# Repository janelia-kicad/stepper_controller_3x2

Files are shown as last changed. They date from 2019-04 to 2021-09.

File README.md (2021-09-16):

- [Repository Information](#orgc9c7126)
  - [Description](#org623a5bf)
- [Images](#org1e7d118)
- [Schematic](#org1bed005)
- [Gerbers](#orga20a872)
- [Bill of Materials](#orgaaed6d6)
  - [PCB Parts](#org5e94890)
  - [Supplemental Parts](#org4c9b4c5)
  - [Vendor Parts Lists](#orge23b973)
- [Supplemental Documentation](#org541ab7a)
  - [Assembly Instructions](#org2701e28)

# Repository Information

-   **Name:** stepper\_controller\_3x2
-   **Version:** 1.2
-   **License:** Open-Source Hardware
-   **URL:** <https://github.com/janelia-kicad/stepper_controller_3x2>
-   **Author:** Peter Polidoro
-   **Email:** peter@polidoro.io

## Description

This board controls 1 stepper motor with optional forward and reverse limit switches.

# Images

# Schematic

[./schematic/stepper\_controller\_3x2.pdf](./schematic/stepper_controller_3x2.pdf)

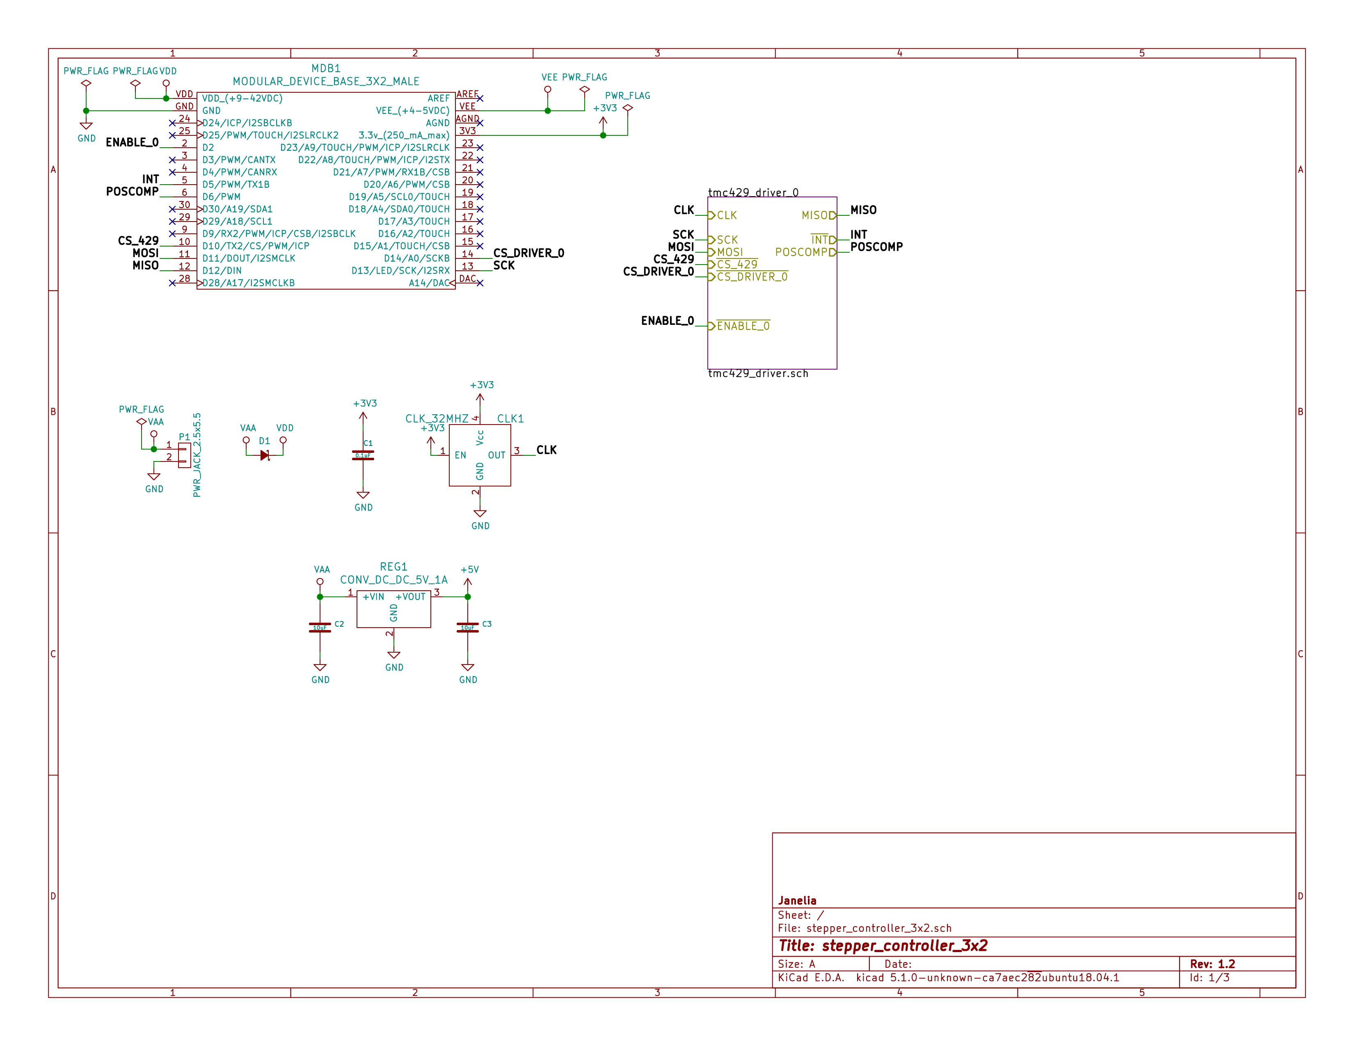
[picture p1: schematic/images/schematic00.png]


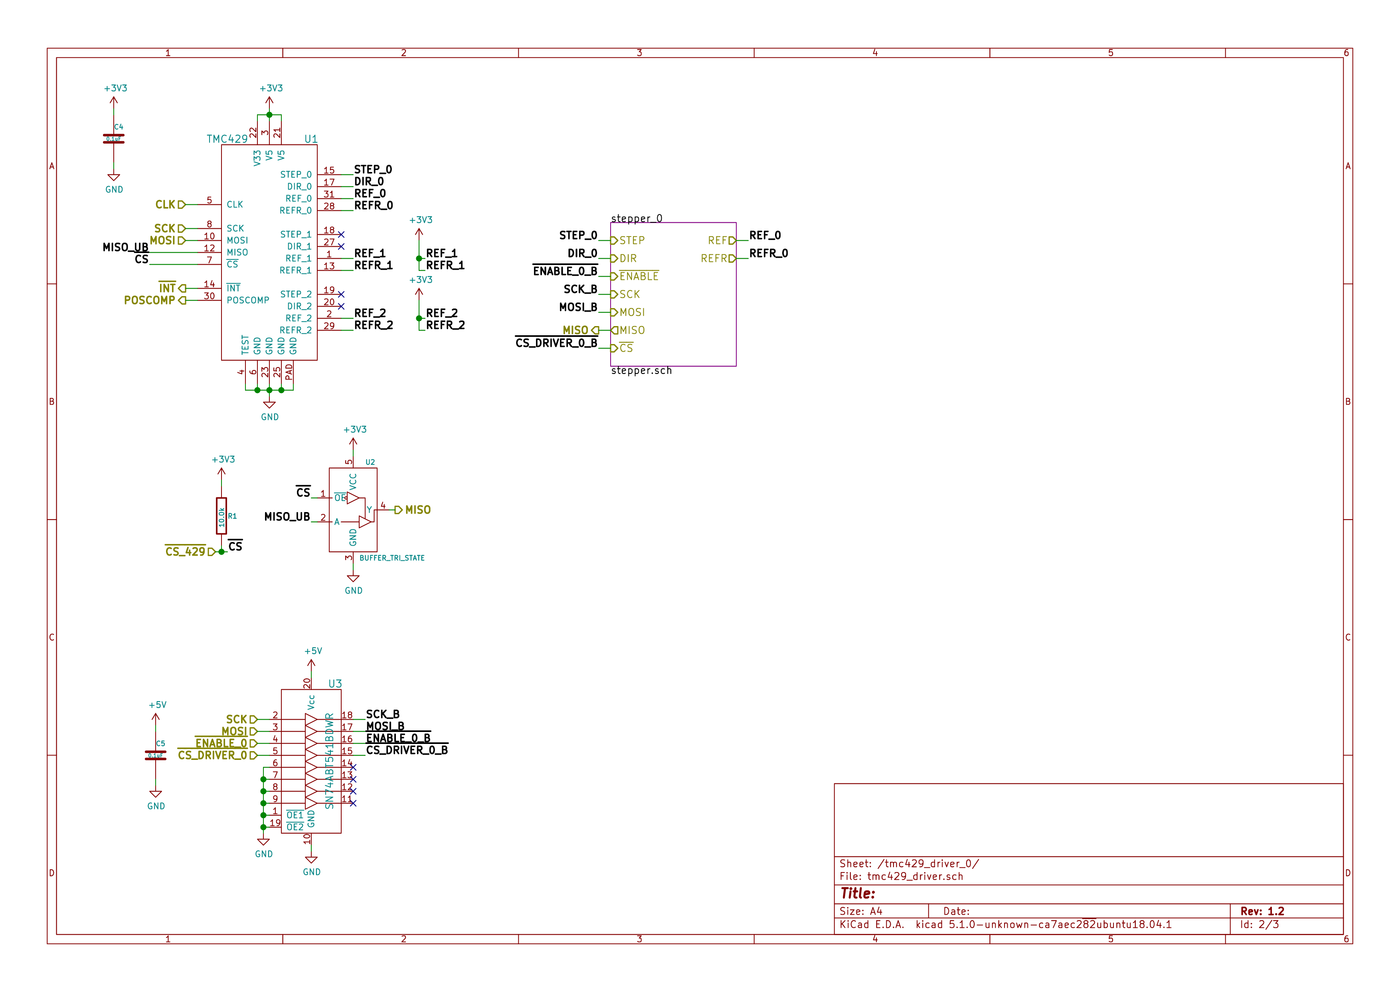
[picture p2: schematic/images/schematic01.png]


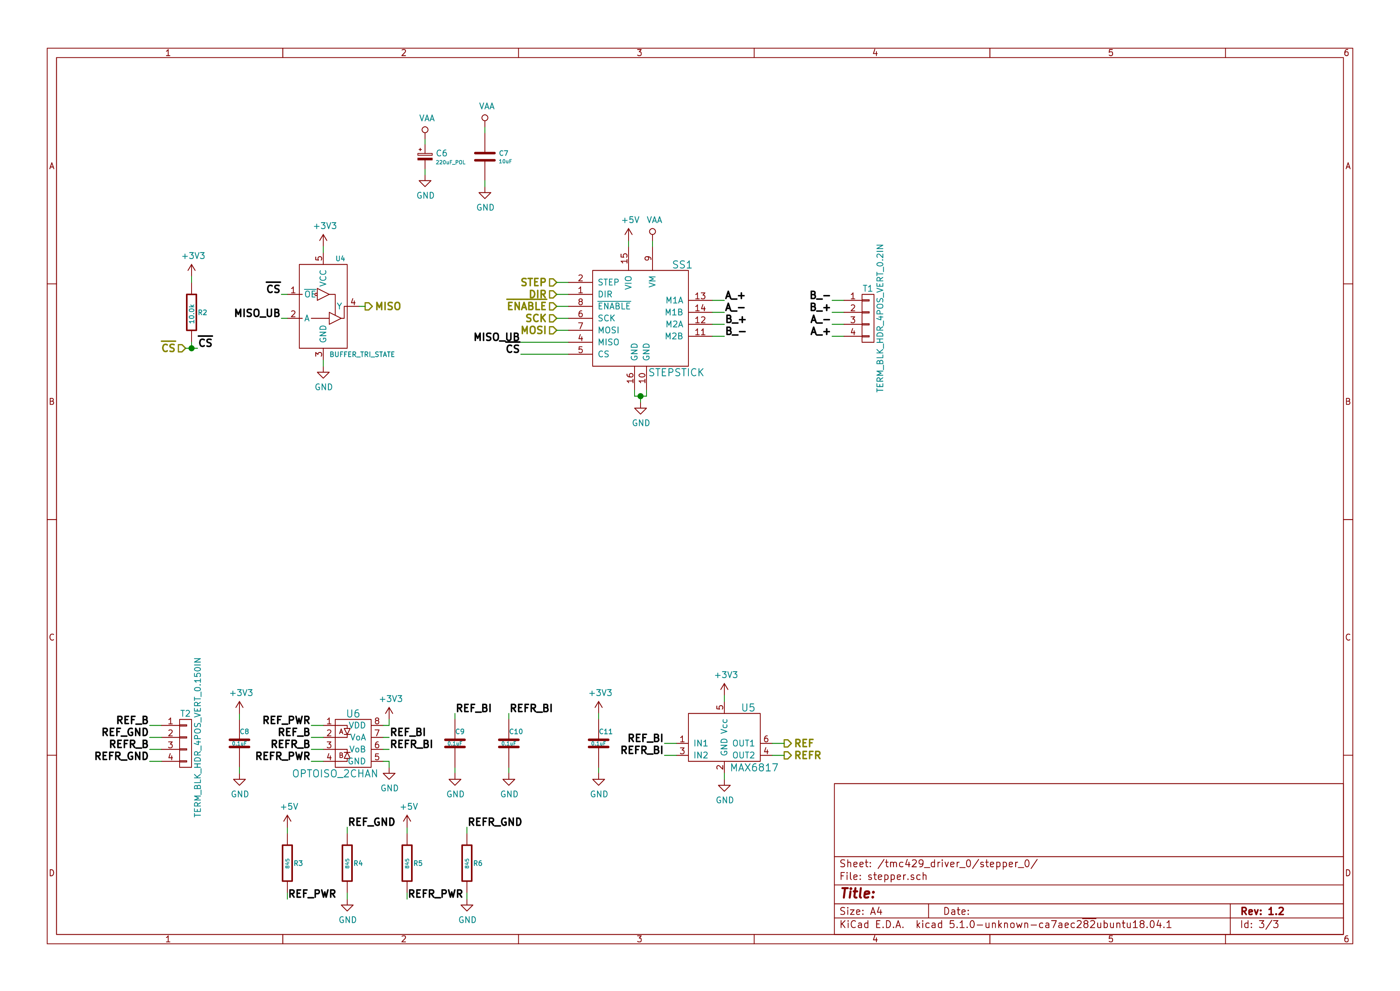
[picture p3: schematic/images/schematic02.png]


# Gerbers

Send gerbers zip file to your favorite PCB manufacturer for fabrication.

[./gerbers/stepper\_controller\_3x2\_v1.2.zip](./gerbers/stepper_controller_3x2_v1.2.zip)

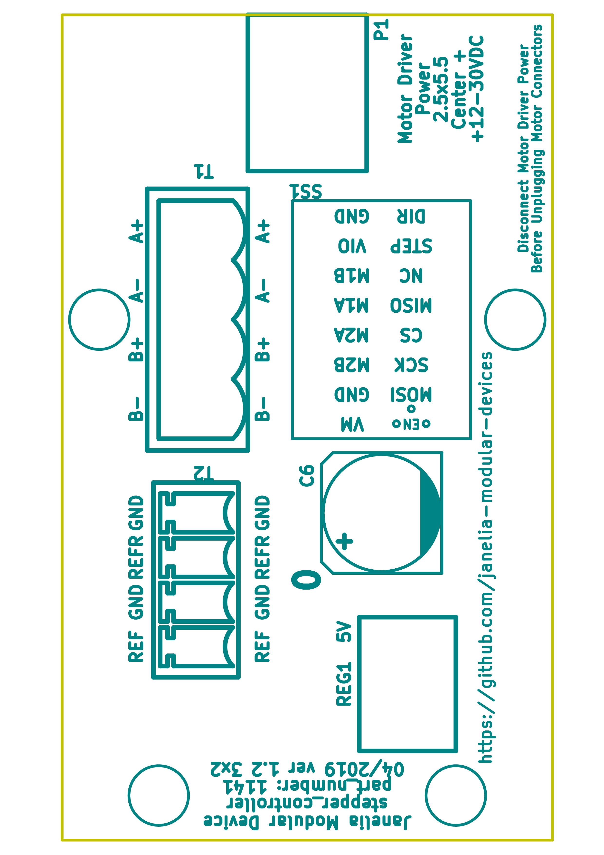
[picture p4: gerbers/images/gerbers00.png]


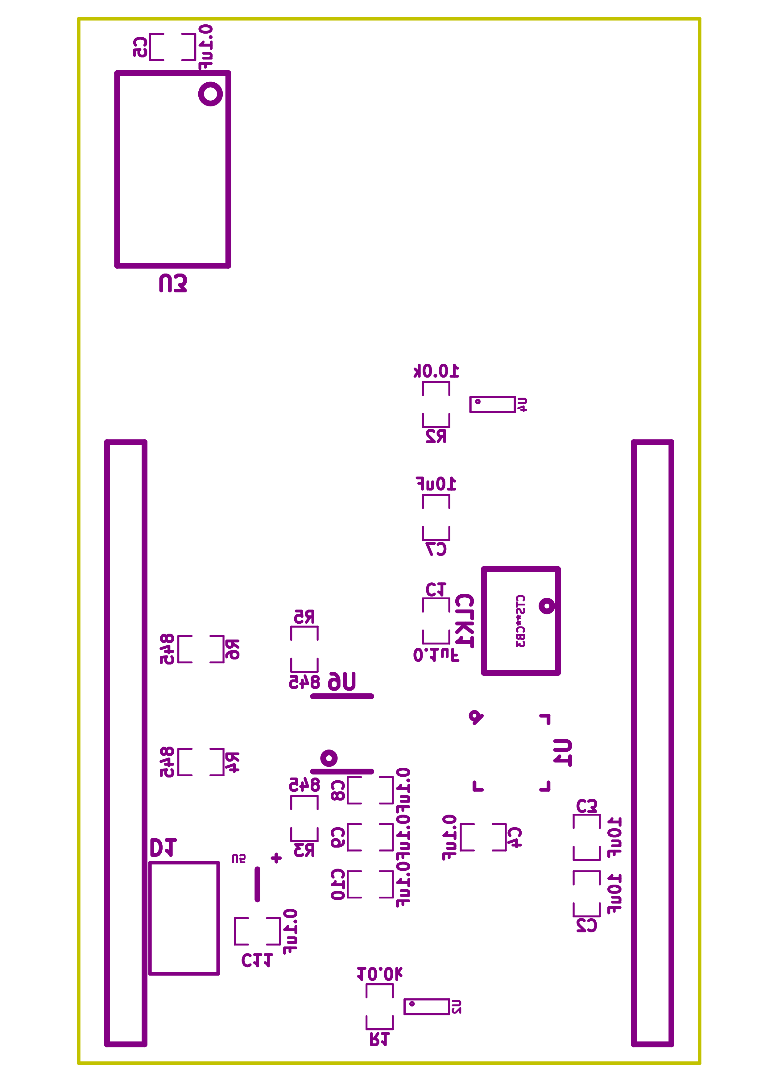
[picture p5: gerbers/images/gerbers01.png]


# Bill of Materials

## PCB Parts

| Item | Reference(s) | Quantity | PartNumber | Vendor  | Description |
|---- |--- |--- |--- |--- |--- |
| 1 | C1 C10 C11 C4 C5 C8 C9 | 7 | 399-14636-1-ND | digikey | CAP CER 0.1UF 50V X7R 0805 |
| 2 | C2 C3 C7 | 3 | 445-14419-1-ND | digikey | CAP CER 10UF 35V X5R 0805 |
| 3 | C6 | 1 | PCE3812CT-ND | digikey | CAP ALUM 220UF 20% 50V SMD |
| 4 | CLK1 | 1 | CTX277LVCT-ND | digikey | OSC XO 32.000MHZ HCMOS TTL SMD |
| 5 | D1 | 1 | 568-11697-1-ND | digikey | DIODE SCHOTTKY 45V 10A CFP15 |
| 6 | MDB1 | 2 | S1011E-16-ND | digikey | 16 Position Header Through Hole Male Pins |
| 7 | P1 | 1 | CP-063BH-ND | digikey | CONN PWR JACK DC 2.5X5.5 8A T/H |
| 8 | R1 R2 | 2 | P10.0KCCT-ND | digikey | RES SMD 10K OHM 1% 1/8W 0805 |
| 9 | R3 R4 R5 R6 | 4 | P845CCT-ND | digikey | RES SMD 845 OHM 1% 1/8W 0805 |
| 10 | REG1 | 1 | 945-1395-5-ND | digikey | CONV DC/DC 1A 5V OUT SIP VERT |
| 11 | SS1 | 16 | ED90331-ND | digikey | CONN PIN RCPT .025-.037 SOLDER |
| 12 | T1 | 1 | 277-1152-ND | digikey | TERM BLOCK HDR 4POS VERT 5.08MM |
| 13 | T2 | 1 | 277-1223-ND | digikey | TERM BLOCK HDR 4POS VERT 3.81MM |
| 14 | U1 | 1 | 1460-1071-1-ND | digikey | IC MOTOR CONTROLLER SPI 32QFN |
| 15 | U2 U4 | 2 | 296-11603-1-ND | digikey | IC BUF NON-INVERT 5.5V SOT23-5 |
| 16 | U3 | 1 | 296-14668-1-ND | digikey | Buffer Non-Inverting 1 Element 8 Bit per Element Push-Pull Output 20-SOIC |
| 17 | U5 | 1 | MAX6817EUT+TCT-ND | digikey | IC DEBOUNCER SWITCH DUAL SOT23-6 |
| 18 | U6 | 1 | 516-2614-1-ND | digikey | OPTOISO 3.75KV 2CH PUSH PULL 8SO |

## Supplemental Parts

| Item | Quantity | PartNumber | Vendor  | Description |
|---- |--- |--- |--- |--- |
| 1 | 1 | 277-1013-ND | digikey | TERM BLOCK PLUG 4POS STR 5.08MM |
| 2 | 1 | 277-1042-ND | digikey | TERM BLOCK PLUG 4POS 5.08MM |
| 3 | 1 | 277-1163-ND | digikey | TERM BLOCK PLUG 4POS STR 3.81MM |
| 4 | 1 | 277-1193-ND | digikey | TERM BLOCK PLUG 4POS 90DEG 3.81MM |
| 5 | 1 | 1460-1187-ND | digikey | TMC2130 STEPPER DRIVER BOARD |
| 6 | 1 | 501100B00000G-ND | digikey | HEATSINK 14-DIP/16-DIP |
| 7 | 1 | 3M10315-ND | digikey | TAPE ADHESIVE TRANSFER 1/2in X5YD |

## Vendor Parts Lists

[./bom/digikey\_parts.csv](./bom/digikey_parts.csv)

[./bom/supplemental\_digikey\_parts.csv](./bom/supplemental_digikey_parts.csv)

# Supplemental Documentation

## Assembly Instructions

-   Solder header pins into the stepper driver board, making note of TOP label. Insert header pins on bottom of board so that the long unsoldered header pins point down when the TOP label faces up.
-   Expose one side of the thermal adhesive tape and attach to the bottom of the heatsink. Trim tape so it does not extend beyond heatsink edges.
-   Expose the other side of the thermal adhesive tape and attach the heatsink to the stepper driver board on the side with the TOP label.
-   Solder surface mount and through hole components onto the pcb.
-   Insert stepper driver board into pin receptacles.

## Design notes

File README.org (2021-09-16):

# Created 2019-04-12 Fri 13:52
#+OPTIONS: title:nil author:nil email:nil toc:t |:t ^:nil
* Repository Information

- Name :: stepper_controller_3x2
- Version :: 1.2
- License :: Open-Source Hardware
- URL :: https://github.com/janelia-kicad/stepper_controller_3x2
- Author :: Peter Polidoro
- Email :: peter@polidoro.io

** Description

This board controls 1 stepper motor with optional forward and reverse
limit switches.

* Images

* Schematic

[[file:./schematic/stepper_controller_3x2.pdf][./schematic/stepper_controller_3x2.pdf]]







* Gerbers

Send gerbers zip file to your favorite PCB manufacturer for fabrication.

[[file:./gerbers/stepper_controller_3x2_v1.2.zip][./gerbers/stepper_controller_3x2_v1.2.zip]]





* Bill of Materials

** PCB Parts

| Item | Reference(s)           | Quantity | PartNumber        | Vendor  | Description                                                               |
|------+------------------------+----------+-------------------+---------+---------------------------------------------------------------------------|
|    1 | C1 C10 C11 C4 C5 C8 C9 |        7 | 399-14636-1-ND    | digikey | CAP CER 0.1UF 50V X7R 0805                                                |
|    2 | C2 C3 C7               |        3 | 445-14419-1-ND    | digikey | CAP CER 10UF 35V X5R 0805                                                 |
|    3 | C6                     |        1 | PCE3812CT-ND      | digikey | CAP ALUM 220UF 20% 50V SMD                                                |
|    4 | CLK1                   |        1 | CTX277LVCT-ND     | digikey | OSC XO 32.000MHZ HCMOS TTL SMD                                            |
|    5 | D1                     |        1 | 568-11697-1-ND    | digikey | DIODE SCHOTTKY 45V 10A CFP15                                              |
|    6 | MDB1                   |        2 | S1011E-16-ND      | digikey | 16 Position Header Through Hole Male Pins                                 |
|    7 | P1                     |        1 | CP-063BH-ND       | digikey | CONN PWR JACK DC 2.5X5.5 8A T/H                                           |
|    8 | R1 R2                  |        2 | P10.0KCCT-ND      | digikey | RES SMD 10K OHM 1% 1/8W 0805                                              |
|    9 | R3 R4 R5 R6            |        4 | P845CCT-ND        | digikey | RES SMD 845 OHM 1% 1/8W 0805                                              |
|   10 | REG1                   |        1 | 945-1395-5-ND     | digikey | CONV DC/DC 1A 5V OUT SIP VERT                                             |
|   11 | SS1                    |       16 | ED90331-ND        | digikey | CONN PIN RCPT .025-.037 SOLDER                                            |
|   12 | T1                     |        1 | 277-1152-ND       | digikey | TERM BLOCK HDR 4POS VERT 5.08MM                                           |
|   13 | T2                     |        1 | 277-1223-ND       | digikey | TERM BLOCK HDR 4POS VERT 3.81MM                                           |
|   14 | U1                     |        1 | 1460-1071-1-ND    | digikey | IC MOTOR CONTROLLER SPI 32QFN                                             |
|   15 | U2 U4                  |        2 | 296-11603-1-ND    | digikey | IC BUF NON-INVERT 5.5V SOT23-5                                            |
|   16 | U3                     |        1 | 296-14668-1-ND    | digikey | Buffer Non-Inverting 1 Element 8 Bit per Element Push-Pull Output 20-SOIC |
|   17 | U5                     |        1 | MAX6817EUT+TCT-ND | digikey | IC DEBOUNCER SWITCH DUAL SOT23-6                                          |
|   18 | U6                     |        1 | 516-2614-1-ND     | digikey | OPTOISO 3.75KV 2CH PUSH PULL 8SO                                          |

** Supplemental Parts

| Item | Quantity | PartNumber       | Vendor  | Description                       |
|------+----------+------------------+---------+-----------------------------------|
|    1 |        1 | 277-1013-ND      | digikey | TERM BLOCK PLUG 4POS STR 5.08MM   |
|    2 |        1 | 277-1042-ND      | digikey | TERM BLOCK PLUG 4POS 5.08MM       |
|    3 |        1 | 277-1163-ND      | digikey | TERM BLOCK PLUG 4POS STR 3.81MM   |
|    4 |        1 | 277-1193-ND      | digikey | TERM BLOCK PLUG 4POS 90DEG 3.81MM |
|    5 |        1 | 1460-1187-ND     | digikey | TMC2130 STEPPER DRIVER BOARD      |
|    6 |        1 | 501100B00000G-ND | digikey | HEATSINK 14-DIP/16-DIP            |
|    7 |        1 | 3M10315-ND       | digikey | TAPE ADHESIVE TRANSFER 1/2in X5YD |

** Vendor Parts Lists

[[file:./bom/digikey_parts.csv][./bom/digikey_parts.csv]]

[[file:./bom/supplemental_digikey_parts.csv][./bom/supplemental_digikey_parts.csv]]

* Supplemental Documentation

** Assembly Instructions

- Solder header pins into the stepper driver board, making note of TOP label.
  Insert header pins on bottom of board so that the long unsoldered header
  pins point down when the TOP label faces up.
- Expose one side of the thermal adhesive tape and attach to the bottom of the
  heatsink. Trim tape so it does not extend beyond heatsink edges.
- Expose the other side of the thermal adhesive tape and attach the heatsink
  to the stepper driver board on the side with the TOP label.
- Solder surface mount and through hole components onto the pcb.
- Insert stepper driver board into pin receptacles.

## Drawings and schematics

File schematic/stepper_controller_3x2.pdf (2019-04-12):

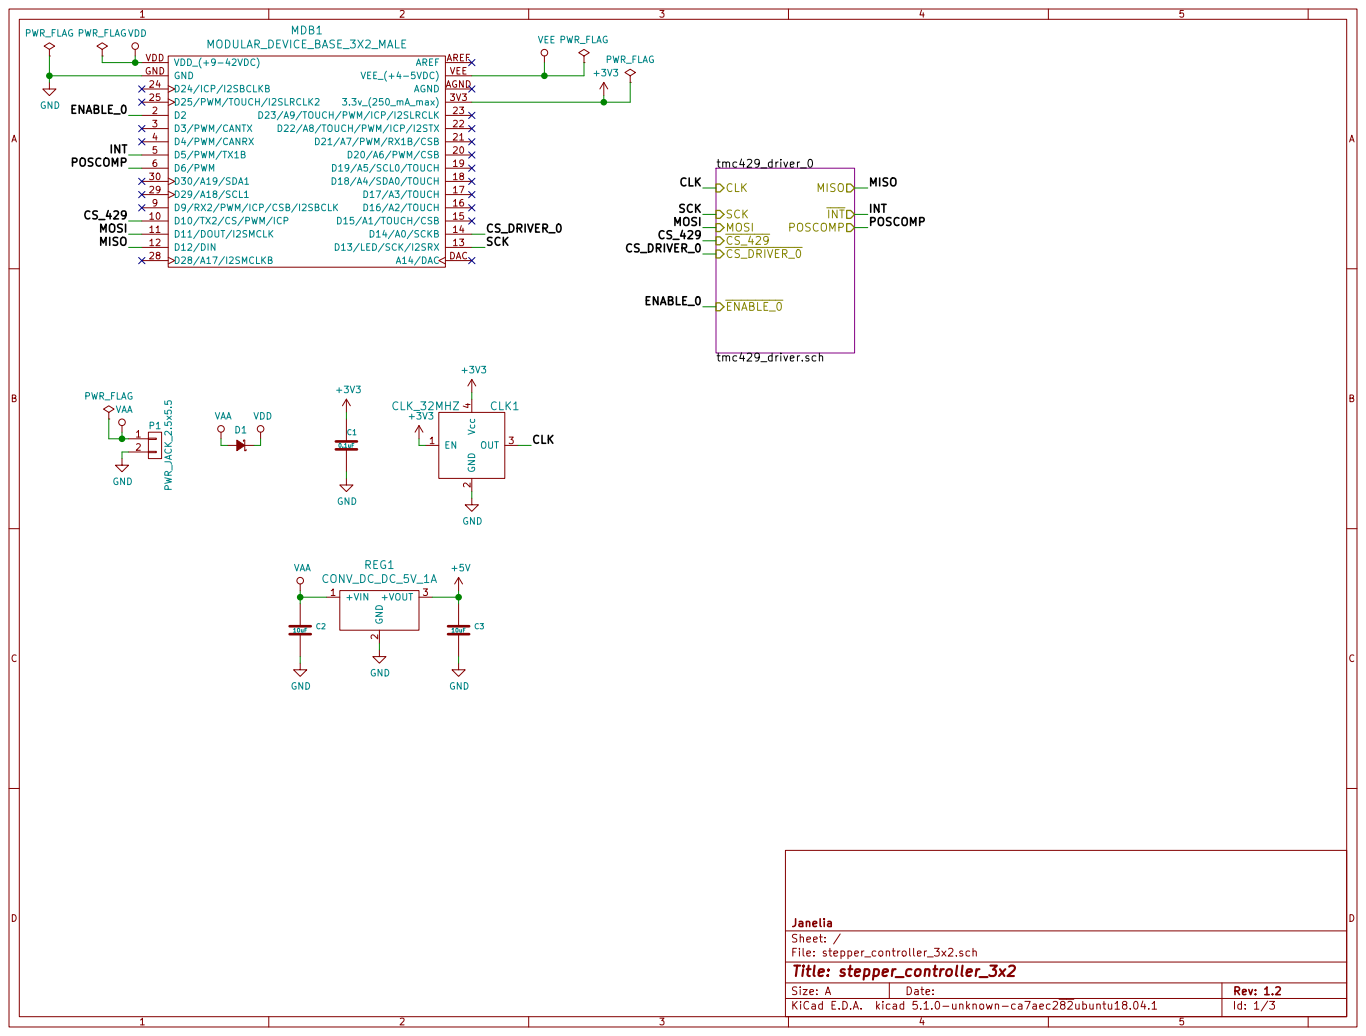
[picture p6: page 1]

File: stepper_controller_3x2.sch Sheet: / Janelia

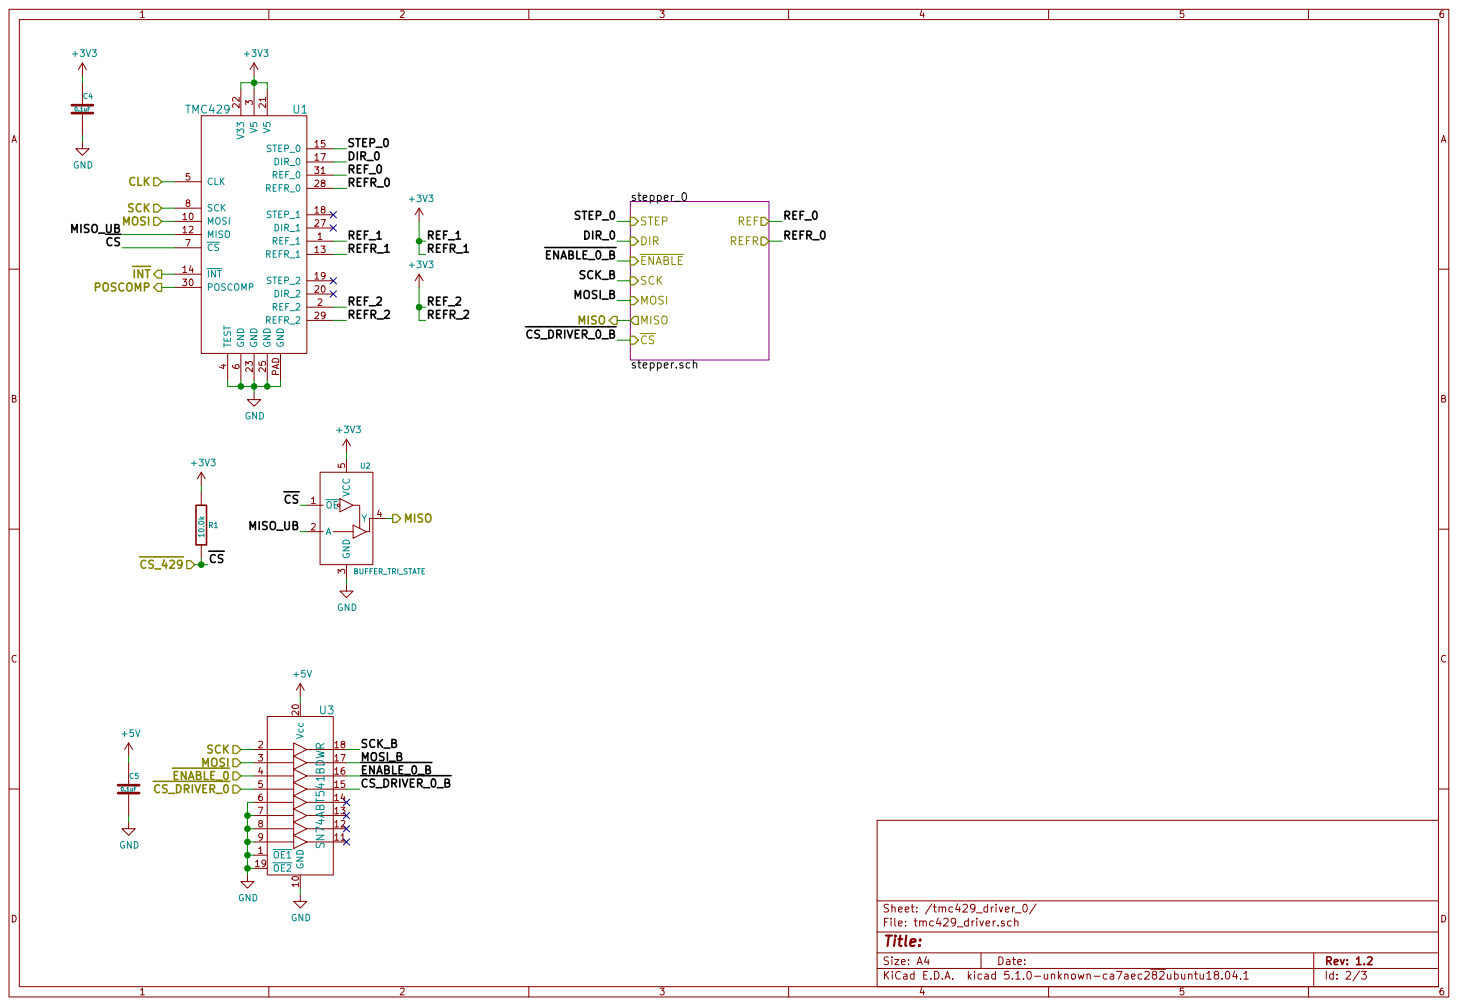
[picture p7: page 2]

6 CS 7 SCK 8 GND PAD

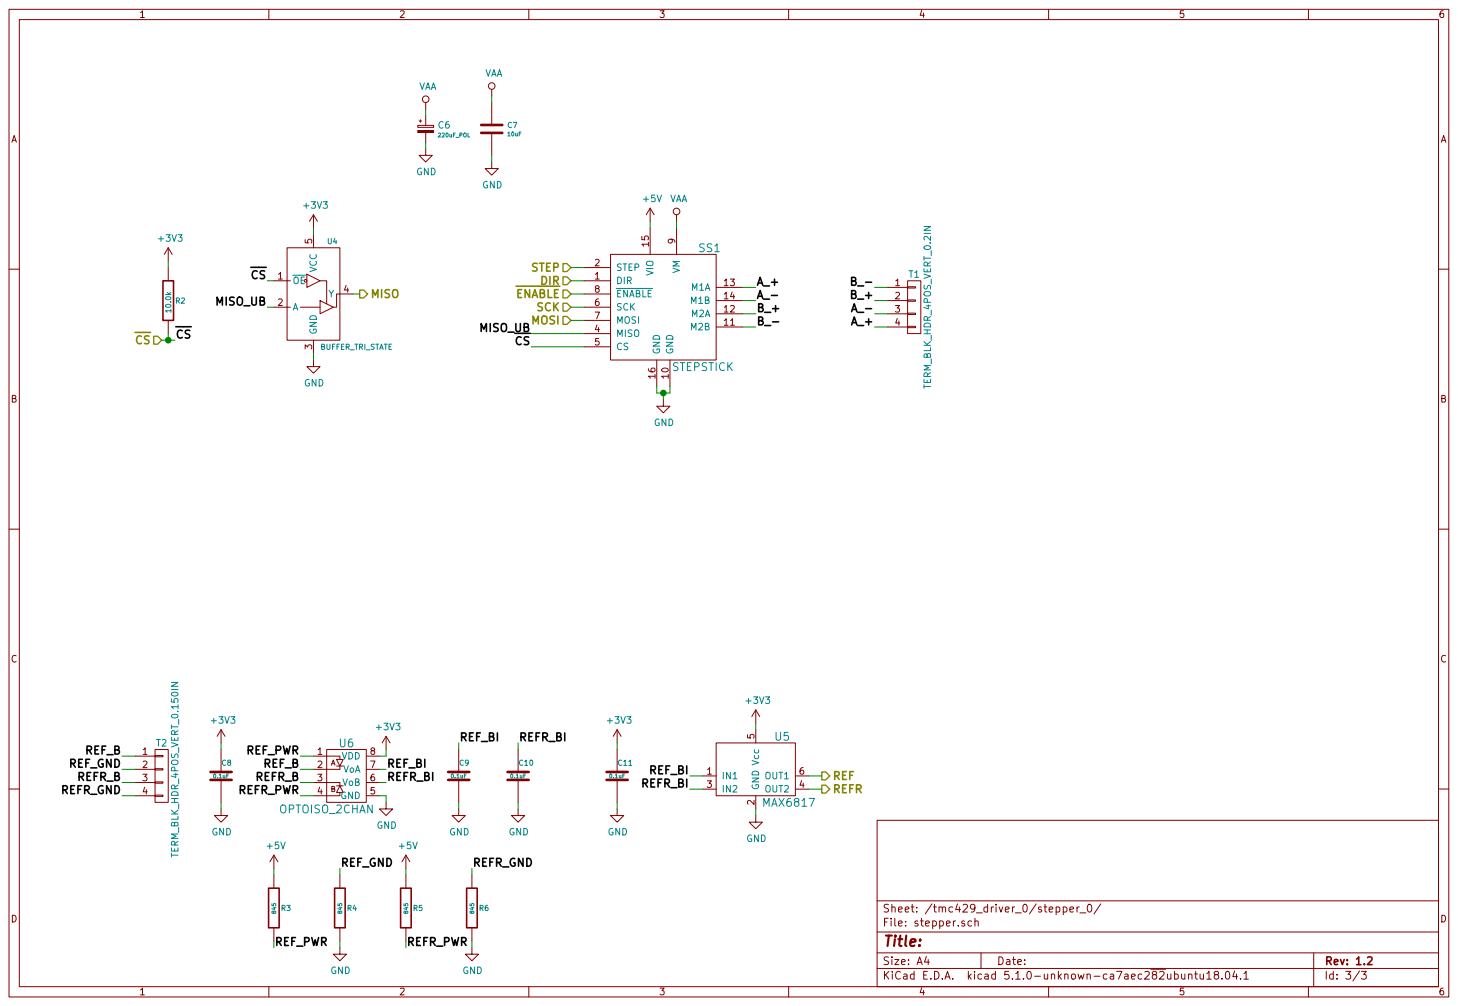
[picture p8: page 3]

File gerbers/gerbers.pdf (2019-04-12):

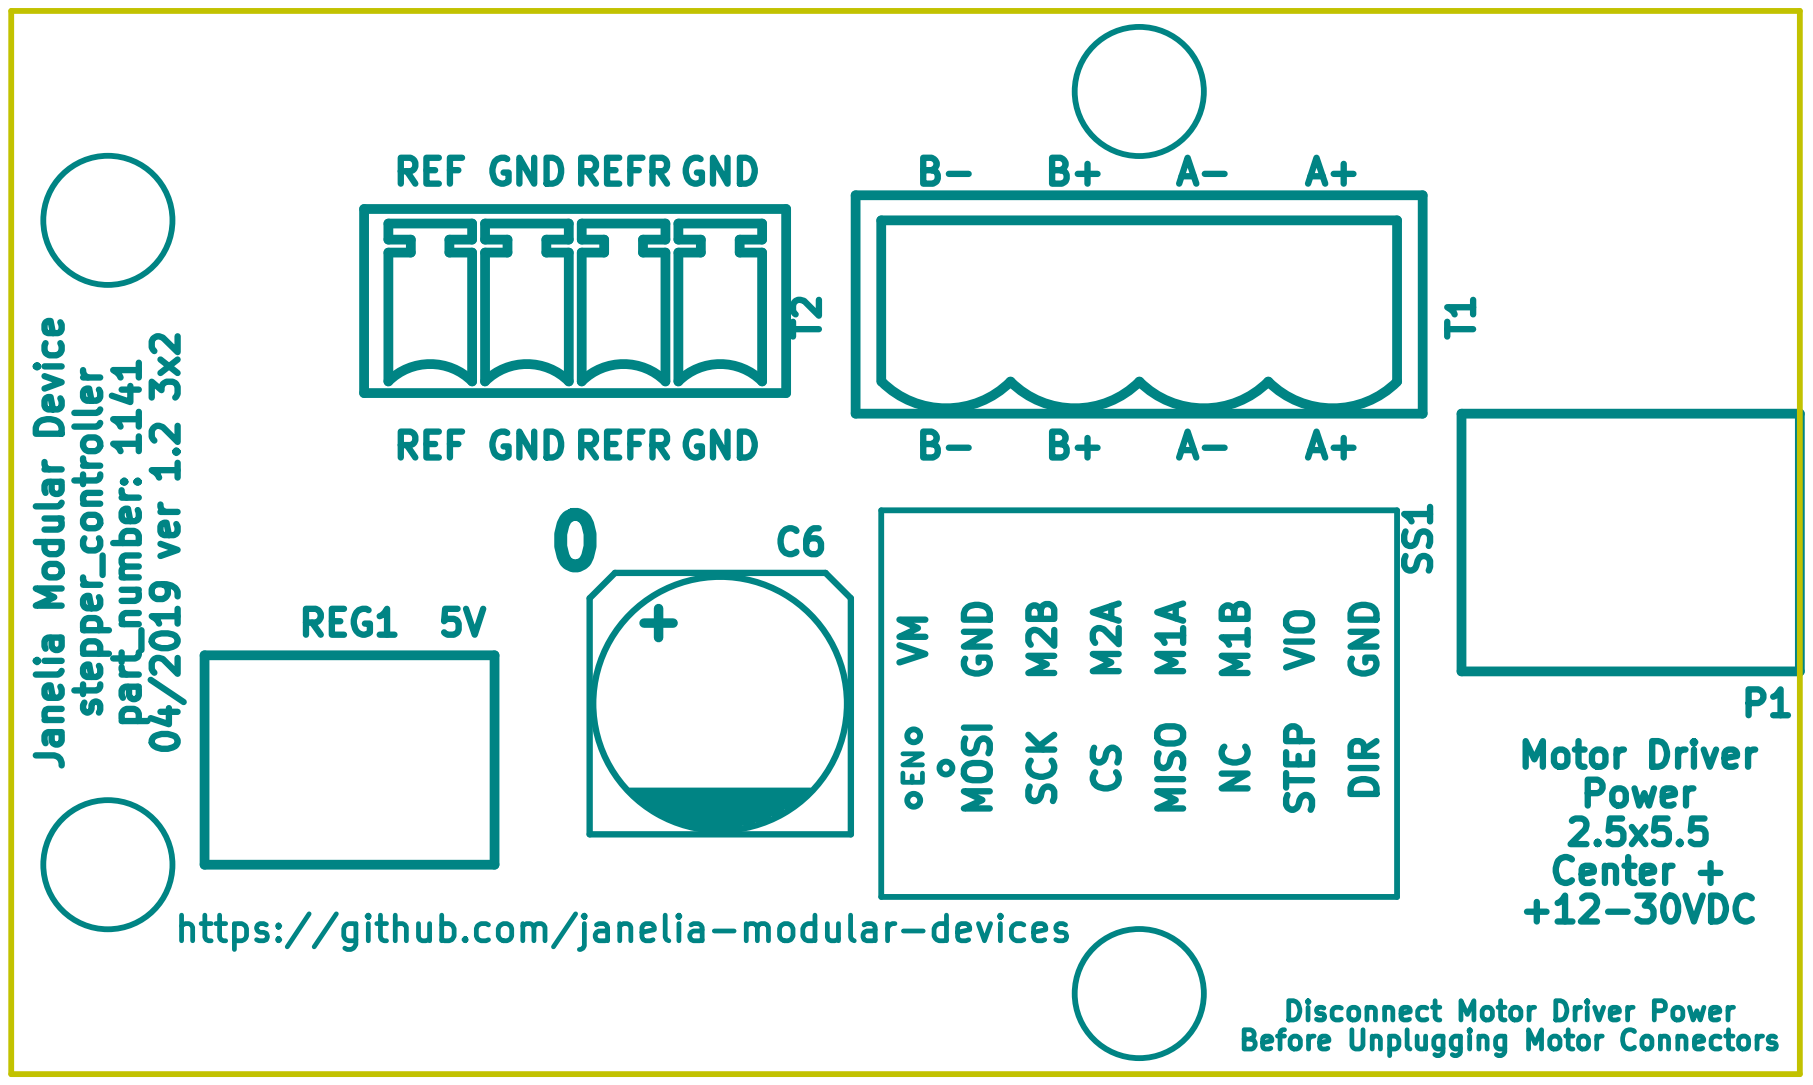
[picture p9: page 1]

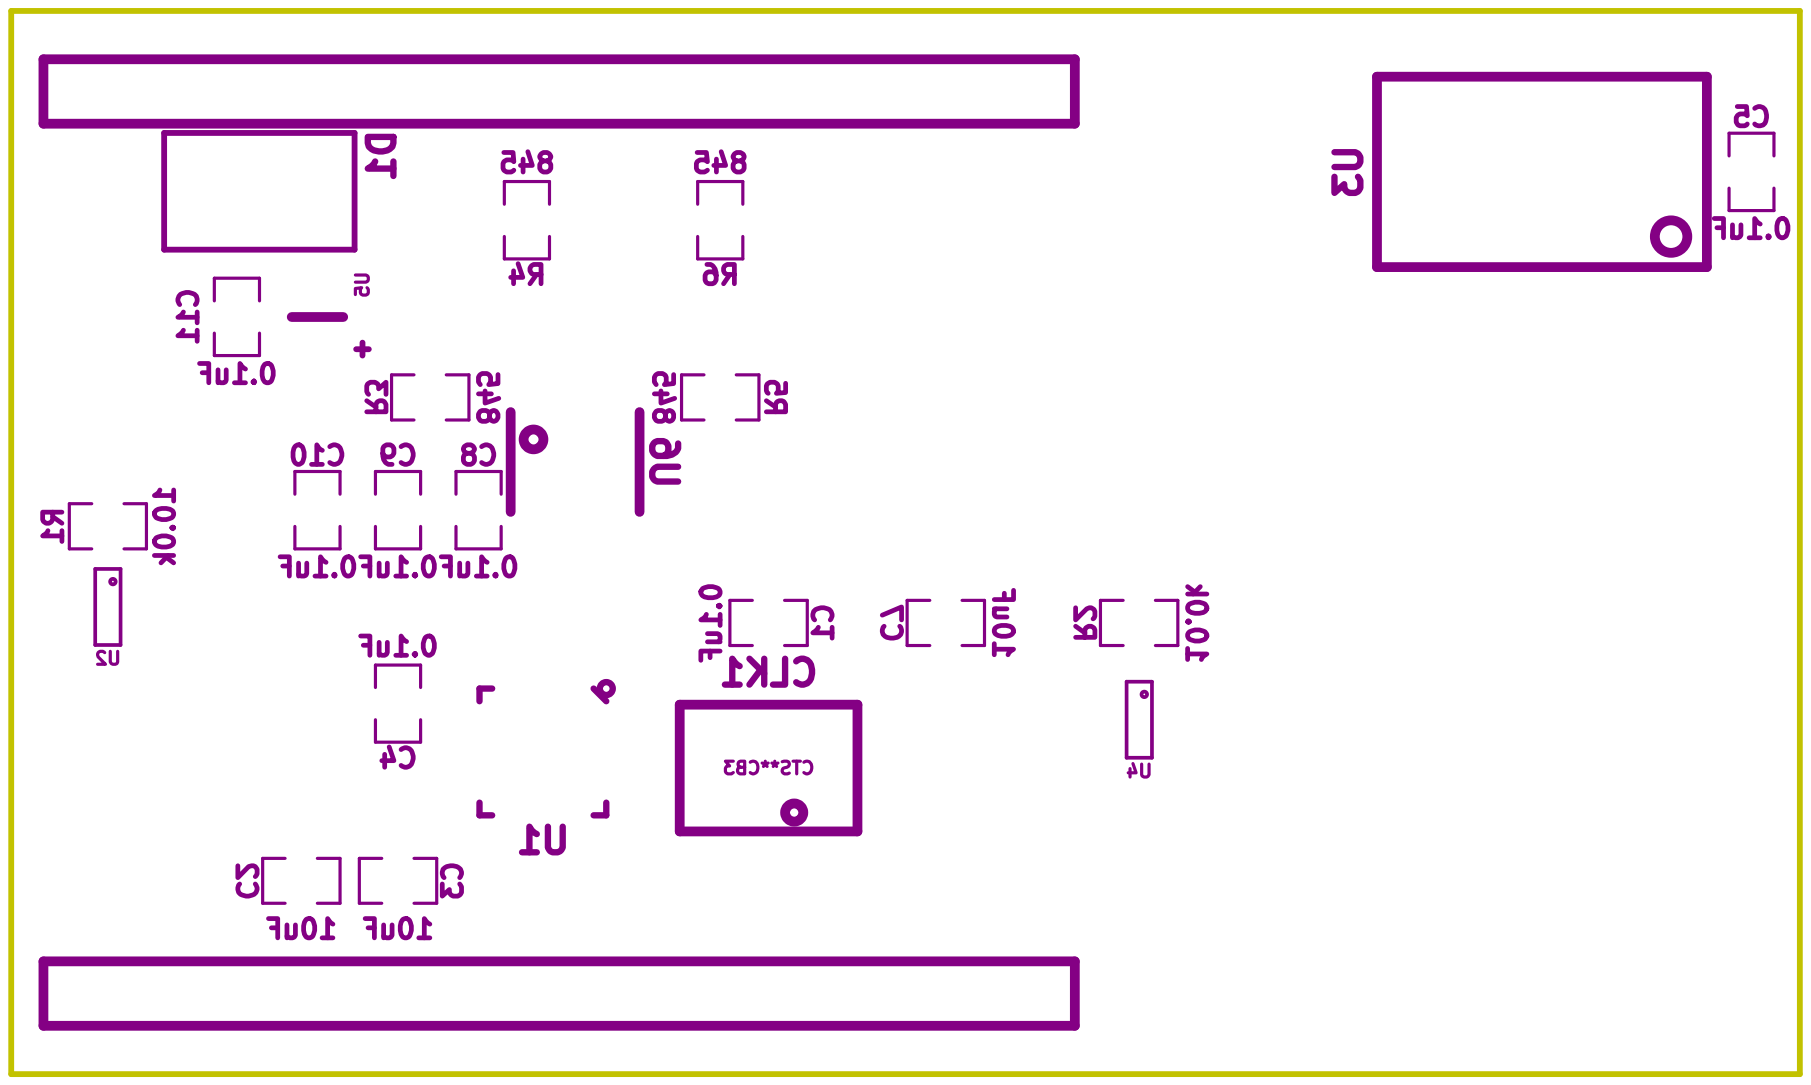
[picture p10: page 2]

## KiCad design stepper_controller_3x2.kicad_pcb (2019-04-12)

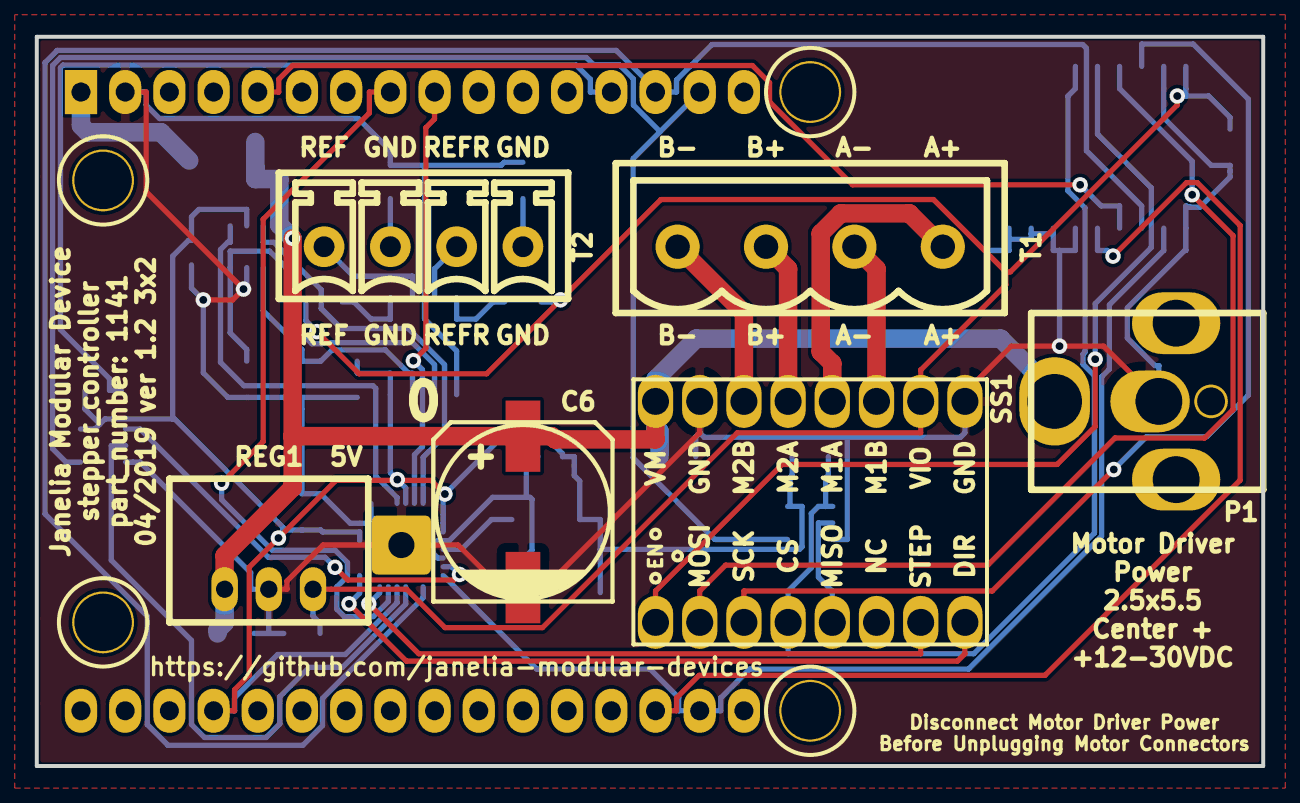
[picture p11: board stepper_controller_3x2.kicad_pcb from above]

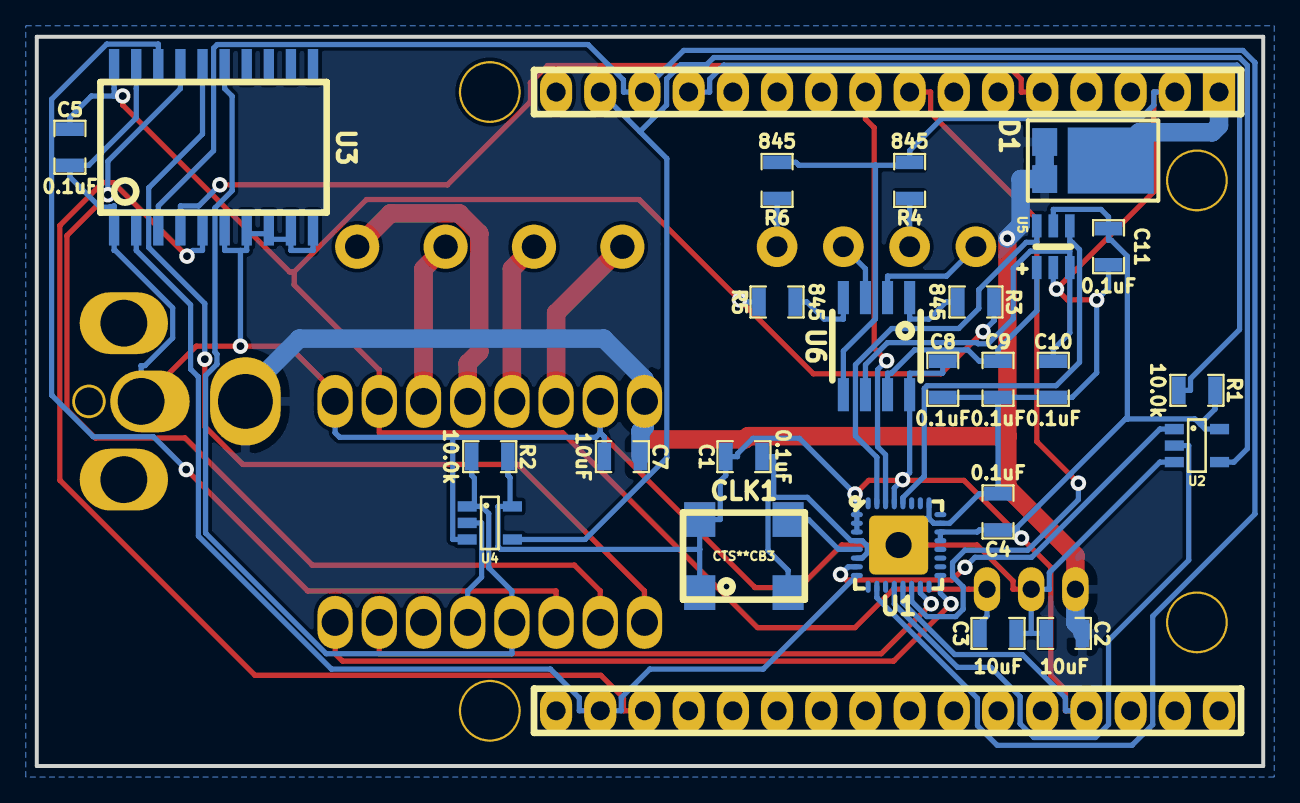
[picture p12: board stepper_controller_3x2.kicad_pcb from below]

Board: 2 copper layers, 70.5 x 41.9 mm, 31 parts (24 on the bottom side), 37 nets.

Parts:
C1, C4, C5, C8, C9, C10, C11: 0.1uF; SM0805
C2, C3, C7: 10uF; SM0805
C6: 220uF_POL; C_ELEC_10
CLK1: CLK_32MHZ; CTS_SMD_4_7X5MM
D1: diode_schottky_45V_10A; CFP15
MDB1: VAL**; MODULAR_DEVICE_BASE_3X2_MALE
P1: PWR_JACK_2.5x5.5; DCJACK_2PIN_HIGHCURRENT
R1, R2: 10.0k; SM0805
R3, R4, R5, R6: 845; SM0805
REG1: CONV_DC_DC_5V_1A; DC_DC_CONV_R78C
SS1: STEPSTICK
T1: TERM_BLK_HDR_4POS_VERT_0.2IN
T2: TERM_BLK_HDR_4POS_VERT_0.150IN
U1: TMC429; QFN-5x5-32
U2, U4: BUFFER_TRI_STATE; SOT-23-5
U3: SN74ABT541BDWR; SOIC_20
U5: VAL**; MAX6817
U6: OPTOISO_2CHAN; SO-8

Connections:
+3V3: C1.1, C4.1, C8.1, C11.1, CLK1.1, CLK1.4, MDB1.3V3, R1.1, R2.1, U1.1, U1.2, U1.3, U1.13, U1.21, U1.22, U1.29, U2.5, U4.5, U5.5, U6.8
+5V: C3.1, C5.1, R3.1, R5.1, REG1.3, SS1.15, U3.20
/CLK: CLK1.3, U1.5
/CS_429: MDB1.10, R1.2
/CS_DRIVER_0: MDB1.14, U3.5
/ENABLE_0: MDB1.2, U3.4
/INT: MDB1.5, U1.14
/MISO: MDB1.12, U2.4, U4.4
/MOSI: MDB1.11, U1.10, U3.3
/POSCOMP: MDB1.6, U1.30
/SCK: MDB1.13, U1.8, U3.2
/tmc429_driver_0/DIR_0: SS1.1, U1.17
/tmc429_driver_0/MISO_UB: U1.12, U2.2
/tmc429_driver_0/MOSI_B: SS1.7, U3.17
/tmc429_driver_0/REFR_0: U1.28, U5.4
/tmc429_driver_0/REF_0: U1.31, U5.6
/tmc429_driver_0/SCK_B: SS1.6, U3.18
/tmc429_driver_0/STEP_0: SS1.2, U1.15
/tmc429_driver_0/stepper_0/A_+: SS1.13, T1.4
/tmc429_driver_0/stepper_0/A_-: SS1.14, T1.3
/tmc429_driver_0/stepper_0/B_+: SS1.12, T1.2
/tmc429_driver_0/stepper_0/B_-: SS1.11, T1.1
/tmc429_driver_0/stepper_0/MISO_UB: SS1.4, U4.2
/tmc429_driver_0/stepper_0/REFR_B: T2.3, U6.3
/tmc429_driver_0/stepper_0/REFR_BI: C10.1, U5.3, U6.6
/tmc429_driver_0/stepper_0/REFR_GND: R6.1, T2.4
/tmc429_driver_0/stepper_0/REFR_PWR: R5.2, U6.4
/tmc429_driver_0/stepper_0/REF_B: T2.1, U6.2
/tmc429_driver_0/stepper_0/REF_BI: C9.1, U5.1, U6.7
/tmc429_driver_0/stepper_0/REF_GND: R4.1, T2.2
/tmc429_driver_0/stepper_0/REF_PWR: R3.2, U6.1
/tmc429_driver_0/~CS: U1.7, U2.1
/tmc429_driver_0/~CS_DRIVER_0_B: R2.2, SS1.5, U3.15, U4.1
/tmc429_driver_0/~ENABLE_0_B: SS1.8, U3.16
GND: C1.2, C2.2, C3.2, C4.2, C5.2, C6.2, C7.2, C8.2, C9.2, C10.2, C11.2, CLK1.2, MDB1.GND, P1.2, R4.2, R6.2, REG1.2, SS1.10, SS1.16, U1.4, U1.6, U1.23, U1.25, U1.PAD, U2.3, U3.1, U3.6, U3.7, U3.8, U3.9, U3.10, U3.19, U4.3, U5.2, U6.5
VAA: C2.1, C6.1, C7.1, D1.2, P1.1, REG1.1, SS1.9
VDD: D1.1, MDB1.VDD

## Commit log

2017-03-29 Initial commit.
    [bom_pcb.csv, bom_pcb_add.csv, digikey_order.csv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]
2017-03-29 Renamed files.
    [stepper.sch, stepper_controller_3x2.sch, tmc429_tmc260.sch]
2017-03-29 Removed footprint.
    [stepper_controller_3x2.kicad_pcb]
2017-03-30 Renamed tmc260 -> tmc26x.
    [stepper_controller_3x2.sch, tmc429_tmc26x.sch]
2017-03-30 Added TERM_BLK_HDR_4POS_VERT_0.150IN.kicad_mod.
2017-03-30 Updated bom.
    [bom_pcb_add.csv, digikey_order_pcb_add.csv]
2017-03-31 Moved pin.
    [stepper.sch]
2017-03-31 First attempt at layout.
    [stepper.sch, stepper_controller_3x2.kicad_pcb, stepper_controller_3x2.sch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]
2017-03-31 Removed extra files.
    [bom_pcb.csv, bom_pcb_add.csv, digikey_order.csv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]
2017-06-15 tmc26x -> driver.
    [stepper_controller_3x2.kicad_pcb, stepper_controller_3x2.sch, tmc429_driver.sch]
2017-06-15 Mostly finished with v1.0.
    [bom_pcb.csv, digikey_order_pcb.csv, stepper.sch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]
2017-06-15 Switched component.
    [stepper.sch, stepper_controller_3x2.sch, tmc429_driver.sch]
2017-06-19 Finished v1.0.
    [bom_pcb.csv, digikey_order.csv, digikey_order_pcb.csv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]
2017-09-13 Updated 0.1uF capacitors.
    [bom_pcb.csv, digikey_order.csv, digikey_order_pcb.csv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]
2017-10-23 Moved footprints.
    [stepper_controller_3x2.kicad_pcb]
2017-10-24 More progress towards v1.1.
    [stepper.sch, stepper_controller_3x2.kicad_pcb, stepper_controller_3x2.sch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]
2017-10-25 Finished version 1.1.
    [bom_pcb.csv, bom_pcb_add.csv, digikey_order.csv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]
2018-01-08 Updated to v4.
    [stepper.sch, stepper_controller_3x2.sch, tmc429_driver.sch]
2018-08-12 Marked extra Teensy pins.
2019-03-28 Progess towards v1.2
    [stepper_controller_3x2.kicad_pcb]
2019-04-02 Progress towards v1.2
    [bom_pcb.csv, bom_pcb_add.csv, digikey_order.csv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]
2019-04-12 Add limit switch filter capacitors
    [digikey_parts.csv, stepper.sch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]
2021-09-21 Remove ignored files
    [stepper_controller_3x2.dsn]
